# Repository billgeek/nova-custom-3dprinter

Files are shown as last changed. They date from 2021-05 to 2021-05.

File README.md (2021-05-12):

# "Nova"
Nova is an Ender 5 Plus inspired 3D printer. While I "borrowed" some ideas of the movements, I designed the entire printer using Sketchup.



## Specifications
- Build volume: 310mm x 310mm x 350mm
- TMC2209 step motor drivers
- 0.9 degree NEMA17 stepper motors (X and Y axes)
- Direct Drive assembly 
- SKR 1.4 Turbo mainboard
- TFT35 Touch Screen display
- External MOSFET components to power the hotend and the heated bed
- Sensorless homing

## Bill of Materials
See the below Google Sheet for the bill of materials:

https://docs.google.com/spreadsheets/d/1B5keSqVwSLgc5OjsFatlqAnYNtMWsLssTLB85XMptbM/edit?usp=sharing

## Build Process
You can find the build instructions in this repo at the following location:
https://github.com/billgeek/nova-custom-3dprinter/tree/main/Build%20Instructions

Alternatively you can follow the Google Docs version of the same instructions:
https://docs.google.com/document/d/1tVqh7jPagdjaWtX-vD9JAcbRu_ECWRMzhDe-mzgvMuw/edit?usp=sharing

## Printed Parts
Please refer to the Bill of Materials sheet linked above for a list of printed parts. The STL files can be found here:
https://github.com/billgeek/nova-custom-3dprinter/tree/main/STL

## Firmware
I used the 2.0.x branch of Marlin when building the firmware for the printer. The configuration files are stored here in this repository.

## Gallery
I've uploaded a few pics to Google Photos during and after the build:

https://photos.app.goo.gl/cp9zkkoZYTewc5xc9

## Lessons Learned
This project taught me a lot of how printers and electronics work in general. Below are some takeaways I think are worth mentioning:
- Not all proximity sensors are made equal! The PL08-N sensors I received operate slightly differently than the standard "round" sensors and as such, I have the light permanently on due to disabling pull-up resistors.
- Squareness of the frame is critical. If your frame is not square, you will guaranteed not have decent quality. Use a T-square or something similar to ensure your build is perfectly square.
- On the SKR1.4, instead of using one driver for both Z motors, I decided to use E1 (second extruder) to drive the second Z motor. This is actually super easy to do, take a look at the included config.
- Instead of setting firmware to invert some axes, I decided to swap pins instead. Inverting in firmware works, but I didn't want to reflash yet again.
- ALWAYS make sure you test your ABL probe on a breadboard or any other way without connecting it to your printer. I had made a mistake with my initial voltage divider and measured 8V from the probe. Had this been installed, I would've fried my SKR!
- The power supply I ordered only has two DC outputs, so I chose to use one output for only the heated bed and the other for the hotend heater and the mainboard.
- The MOSFET modules are absolutely essential when using an SKR board. These boards have integrated MOSFETs for the heated bed and hotend, but they're rated at 10A max. With my bed at 240W and using 24V, that would put me right at the maximum current rating. I'd rather replace a $15 module than a $85 board!

## Still to do
There are a few things I have yet to fix:
- [ ] I need to install some drag chains so the "umbilical cord" stops dragging against the steel rods and to look somewhat better.
- [ ] Design a new electronics enclosure to move the box hanging from the side to the bottom, similar to the Ender 5 setup.
- [ ] Due to how the movements work, I can add Foamboard to the back, left and front with minimal effort to make an enclosure, but I'll still need to create a hood / roof for the X/Y axes.

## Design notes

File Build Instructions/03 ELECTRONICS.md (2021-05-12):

# Electronics

I'm not going to go into detail on how to install electronics for a 3D printer as there are so many detailed articles and videos on the subject available online. Instead, here's a quick to-do list of what I had to do:

- [ ] Install the hotend assembly and extruder of your choice. I went for an assembled Ender 3 hotend (future upgrade opportunity here!) and the Hero Me Gen 5 system with direct drive configuration found here: https://www.thingiverse.com/thing:4460970
- [ ] Optionally install your ABL, inductive probe, proximity sensor or BLTouch of choice.
- [ ] Print and install an electronics enclosure of your choice. There are plenty to choose from on Thingiverse, but I decided to use this one: https://www.thingiverse.com/thing:4338524
- [ ] Install your Mainboard and Mosfets into the enclosure.
- [ ] Wire up all five motors (X, Y, extruder and dual Z) to the mainboard.
- [ ] Print and install an LCD cover of your choice. There are plenty to choose from on Thingiverse, but I decided to use this one: https://www.thingiverse.com/thing:4547059
- [ ] Install your LCD into the cover, attach the cover to the frame and connect it to the mainboard.
- [ ] Wire your Power Supply to the mainboard and MOSFET boards.
- [ ] Connect your hotend and heated bed to the MOSFETs.
- [ ] Optionally connect your ABL to the mainboard.

If all went well, you should now have a semi-operational 3D printer!

The final step in the process would be to download, configure and flash the Firmware of your choice. I'm using Marlin and have included the configuration files I used in this repository.

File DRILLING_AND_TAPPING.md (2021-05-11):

# Drilling and Tapping

You will need to drill and tap holes into the aluminum extrusion. As this is not a handyman writeup but instead a 3D printer build instruction, I'll skip over  _how_ and focus on _what_.

## Materials

- [ ] 4 x 2040 Extrusion @ 500mm - Uprights
- [ ] 8 x 2020 Extrusion @ 500mm - Top and Bottom sides
- [ ] 1 x 2020 Extrusion @ 600mm - X Axis
- [ ] 2 x 2020 Extrusion @ 450mm - Bed Platform
- [ ] 2 x 2020 Extrusion @ 500mm - Bed Platform

### Uprights
**2040 Extrusion 500mm**
- Using an M5 tap, create threads for both center holes on one side and only one of the center holes on the other side. (3 tapped center holes)



### Top and Bottom Sides (only six pieces, leave 2 for later)
**2020 Extrusions 500mm**
- Drill an M5 hole in six of the 2020 500mm extrusions 10mm from either of the edges.



### X-Axis
**2020 Extrusion 600mm**
- From the left side, drill two M5 holes: one at 22mm and the other at 65mm. 
- From the right side, drill two  M5 holes: one at 25mm and the other at 65mm from the right edge.



### Bed Platform

Before we do the bed platform you will need to measure the distance from the center of the holes of your heated bed. This measurement will dictate where the holes will be that you need to drill. In my case, I measured **240mm**, so that's the value I'll use here.

**2020 Extrusion 500mm**
- Drill an M5 hole 10mm from either edge on both pieces. (2 holes total per piece)
- Drill an M4 hole 130mm from either edge. (Formula used: Bed Holes = 240mm apart; Length = 500mm, so remainder = 260mm / 2 = 130mm) This hole will be used for the bed screws.

(In the below picture, do NOT drill into your heated bed, this picture simply indciates where the holes are referred to above)



**2020 Extrusion 450mm**
- Drill two M5 holes at 10mm and at 30mm from the left edge and repeat from the right edge. (4 holes total per piece)
- Rotate the extrusion so the new holes will be perpendicular to the holes you have already drilled. (IE: The holes you drilled before should go front to back while the next set of holes are top to bottom)
- Drill two M5 holes 105mm from each side. (Formula used: Bed Holes = 240mm, so 450mm length - 240mm holes = 210mm / 2 = 105mm)
 


And that's all there is to drill and tap. Next you can start with the actual frame construction.

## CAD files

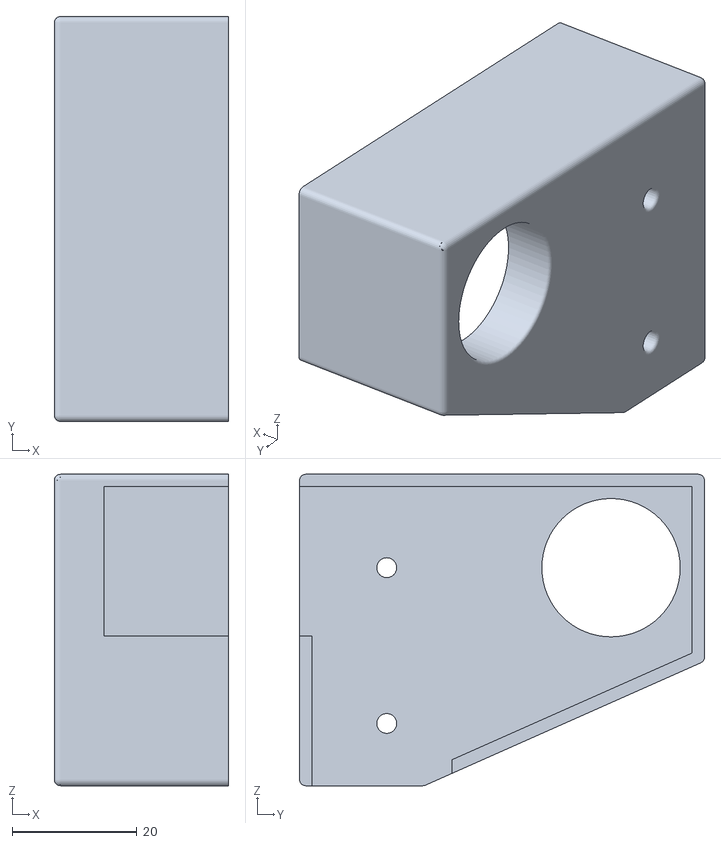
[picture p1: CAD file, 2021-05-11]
STL/YAxisCover.stl
28.0 x 65.0 x 50.0

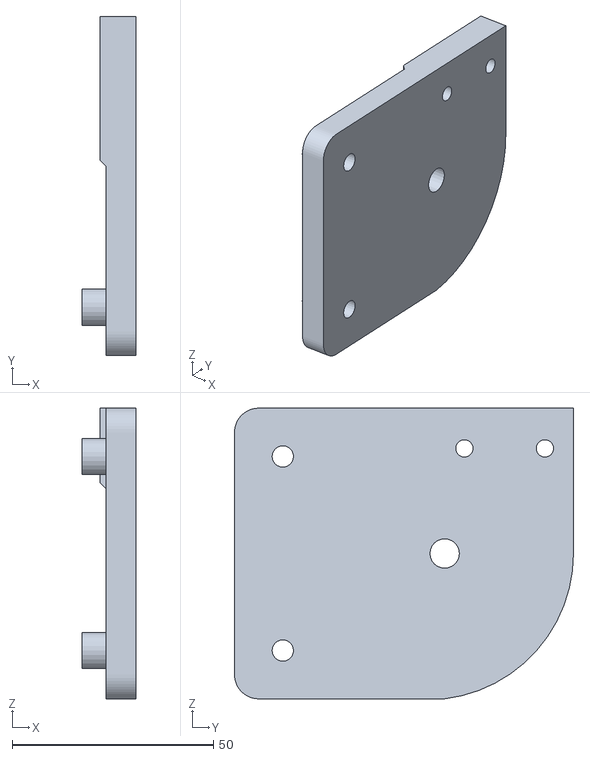
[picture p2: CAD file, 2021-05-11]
STL/ZAxisPlate.stl
13.5 x 84.2 x 72.2

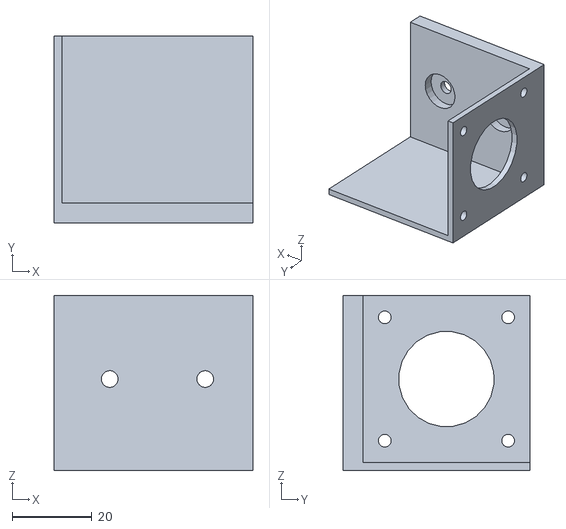
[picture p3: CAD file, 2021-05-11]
STL/YMotorBracket.stl
50.0 x 47.0 x 44.0

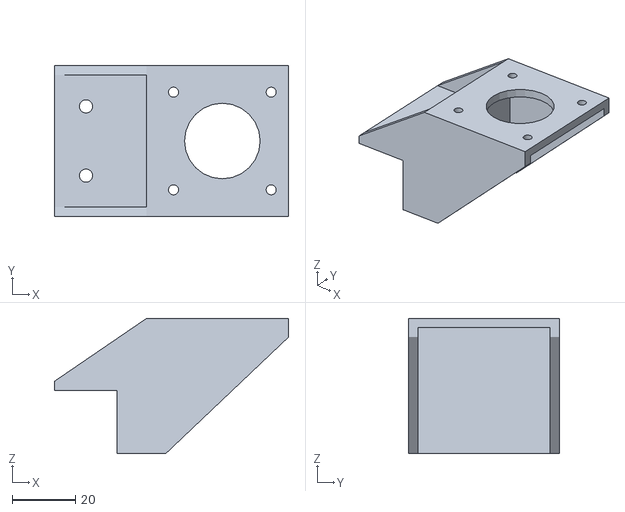
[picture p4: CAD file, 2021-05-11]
STL/ZMotorBracket.stl
74.3 x 48.0 x 43.0

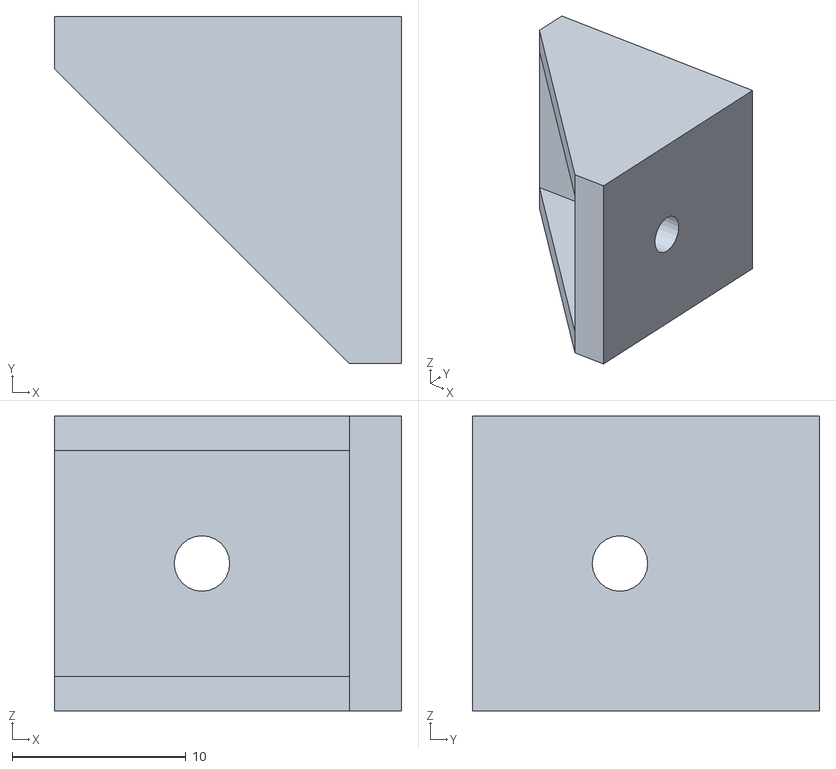
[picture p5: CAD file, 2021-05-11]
STL/UpperAngleBracket.stl
20.0 x 20.0 x 17.0

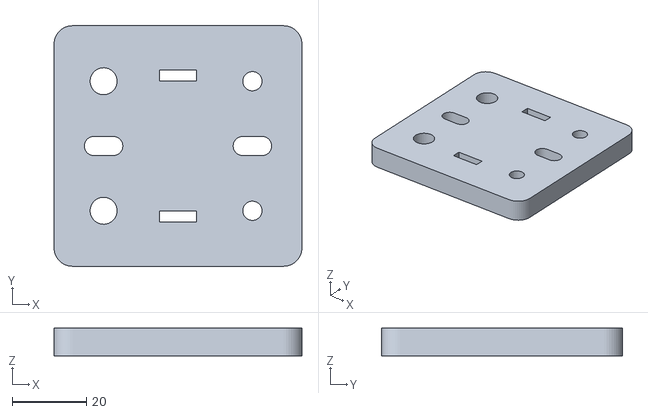
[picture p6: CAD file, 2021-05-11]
STL/XAxisGantryPlate.stl
67.0 x 65.0 x 7.50

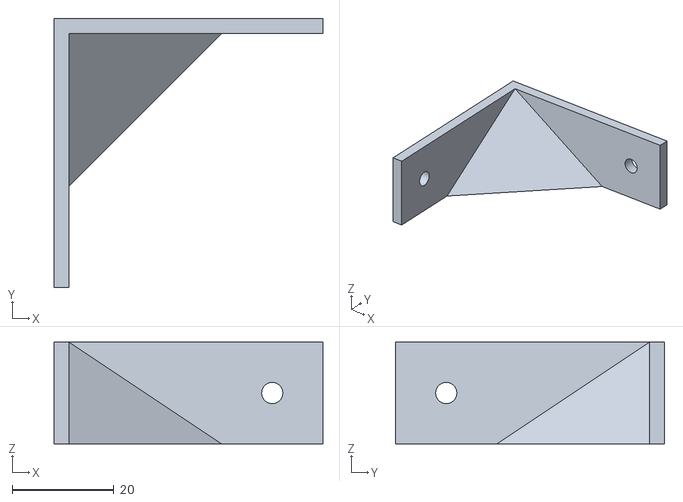
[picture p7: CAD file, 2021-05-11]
STL/LowerAngleBracket.stl
53.0 x 53.0 x 20.0

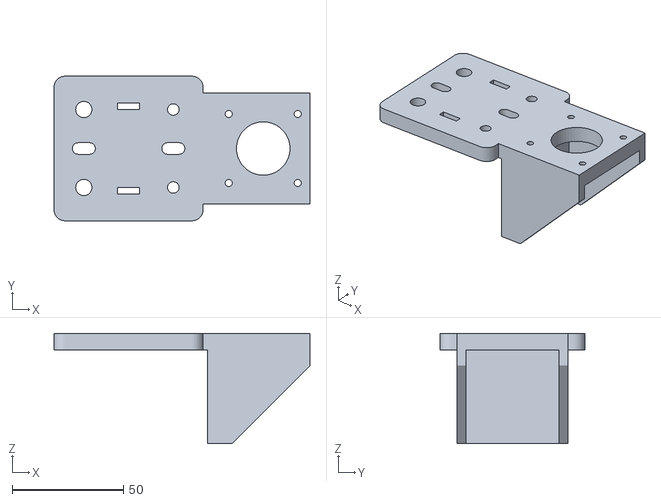
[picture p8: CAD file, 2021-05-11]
STL/XMotorBracket.stl
115.0 x 65.0 x 49.5

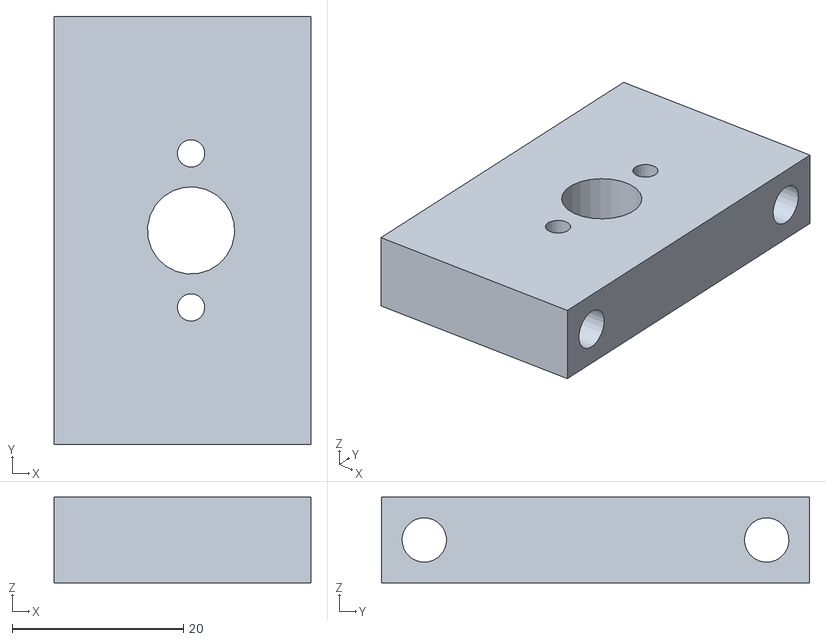
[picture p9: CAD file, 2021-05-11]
STL/LeadScrewNutHolder.stl
30.0 x 50.0 x 10.0

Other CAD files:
Sketchup/Ender 5 Clone.skp

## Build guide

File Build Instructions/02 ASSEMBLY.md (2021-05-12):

# Assembly

For the assembly we'll break it into six sections.

## Frame Base

To assemble the base of the frame:

- Arrange four 2020 extrusions in a square with the front and back between the left and right sides. You will end up with a build that is 540mm wide.
- Attach the four sides together using four printed LowerAngleBracket.stl and two M3x10mm bolts and M3 TNuts per corner.
- Attach the four 2040 extrusions to each corner (two tapped holes facing down AND the one tapped hole facing the inside) using 2 x M5x45mm bolts. Note that the wide sides should face towards the front of the printer.





## Upper Frame
- Arrange four 2020 extrusions in a square with the front and back between the left and right sides.
- Attach the four sides to each-other using the four UpperAngleBracket.stl two M3x10mm bolts and M3 TNuts per corner.
- Temporarily attach the upper frame to the rest of the frame using two M5x45mm bolts through the front and back sections into the tapped upright holes.
- Attach the YMotorBracket.stl to the center of the back section of the upper frame using two M3x10mm bolts and M3 TNuts.
- Attach your dual-shaft stepper motor to the bracket.









## X Axis
- Using the 600mm 2020 extrusion, attach it to the XMotorBracket.stl and XAxisGantryPlate.stl using 4 x M5x45mm bolts and nyloc nuts.
- Attach the stepper motor for the X movement to the motor bracket.
-  Add a toothed pulley to the X Motor.
- Add the hotend gantry plate to the extrusion bar. (You may have to either do this before attaching the X axis plate or remove a POM wheel to "clip" it on)
- Add a smooth pulley into one of the tensioner assemblies and unscrew the tensioner until you have the shortest possible distance. (IE: Allow yourself to pull the belt later)
- Holding the tensioner in place against the end of the X Axis, measure out a belt and attach the belt to the entire assembly.
- Attach four POM wheels to either side of the axis using two eccentric nuts per plate.
- Remove the top frame from the lower frame and slide the X axis over the sides. You may need to remove the "front" bar of the top frame to achieve this.
- Once the X axis is sliding on the top frame, attach the top frame back onto the bottom frame temporarily.





## Build Platform
- Using the remaining two 500mm 2020 extrusions and the two 400mm extrusions, place the shorter ones down and place the longer ones on top at a distance equal to the mounting holes of the bed.
- Attach all the extrusions together using M5 bolts. Do not install your bed yet as there's still work to do and you probably don't want to damage it.
- Attach the two LeadScrewNutHolder.stl to the sides using TNuts. Try to get them exactly in the center, but don't worry too much at this stage, you will likely adjust them later in the build process.
- Install three POM wheels on each of the four ZAxisPlate.stl, taking care to install the single wheel (under the "bump") using an eccentric nut.
- On each end of the sides of extrusion that are "sticking out", attach your assembled ZAxisPlate.stl using M5 bolts and nuts.
- Remove the top frame again and slide the entire bed frame over the corners.
- Once the Z axis is sliding on the corners, attach the top frame back onto the bottom frame temporarily. (Note that this might not be super easy, depending on how accurately you drilled the holes)





## Z Motors and Lead Screws
- Attach a stepper motor to both of the ZMotorBracket.stl
- Attach the stepper motor and bracket assembly to the center of each side on the bottom of the frame. Don't worry about getting this exactly in the center, you will likely have to adjust once the build is more complete.
- Install a coupler on each motor.
- Slide the lead screws through the top of the lead screw nut holder, through the anti-backlash nuts into the coupler. 
- Now move your build platform up and down to it's maximums to adjust everything to the center without tilting. Take your time here to make sure you get it right. I had to redo this a number of times as the build platform kept "tilting" after moving the Z axis down and up again.



## Y Axis
- Remove the top frame from the printer again.
- Insert a 608 bearing into each of the two YAxisCover.stl and set aside for now.
- Place a 5mm to 8mm coupler on each shaft coming out of the Y motor.
- Add a steel shaft to the other side of each coupler and add an 8mm toothed pulley to the other end of each shaft. (Try not to allow them to bend too far as this may cause damage to the couplers)
- With the shaft and pulley installed, attach the Y axis cover using a single M3x10mm bolt and TNut in the top-most hole and add the second M3x10 bolt and T-Nut in the lower hole without attaching it anywhere. Note that the shaft should run parallel to the top-back corner of the frame.
- Once you've installed the covers, install the belts in a similar fashion as you did for the X axis: Hold a tensioner in place against one of the front ends and measure out a belt and attach the belt to the respective gantry plate. Do this on both sides.
- Attach the entire X and Y axis assemblies to the rest of the printer frame using 4 x M5x45mm bolts.
- Complete the attaching of the YAxisCover.stl bottom screw into the side of the 2040 extrusion from the uprights.

## Final Touches
- Install your heated bed to the build platform using the tapered M4 screws, springs and levelling knobs of your choice. (You can either purchase some or find some available on Thingiverse)

Congratulations, you have completed the build! Up next is the Electronics.

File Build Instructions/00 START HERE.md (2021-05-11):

# Nova Custom 3D Printer Build Instructions

There are three main categories to the build instructions, each with a set of steps to complete: Drilling and Tapping, Assembly and Electronics.

Follow each of the links below for a complete assembly:

## Drilling and Tapping

Find the drilling and tapping instructions here: https://github.com/billgeek/nova-custom-3dprinter/blob/main/Build%20Instructions/01%20DRILLING_AND_TAPPING.md

## Assembly

Instructions for assembling all mechanical parts can be found here: https://github.com/billgeek/nova-custom-3dprinter/blob/main/Build%20Instructions/02%20ASSEMBLY.md

## Electronics

There are no detailed instructions for the electronics, but here's a simple to-do list of tasks that need to be completed: https://github.com/billgeek/nova-custom-3dprinter/blob/main/Build%20Instructions/03%20ELECTRONICS.md

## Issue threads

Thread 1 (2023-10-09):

BOM is no longer a valid link

pilotkid, 2023-10-09:
The bill of materials link is broken

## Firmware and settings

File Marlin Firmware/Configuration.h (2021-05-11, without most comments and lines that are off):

#pragma once
#define CONFIGURATION_H_VERSION 020008
#define STRING_CONFIG_H_AUTHOR "(BillGeek, SKR 1.4 Turbo)" // Who made the changes.
#define SHOW_BOOTSCREEN
#define SERIAL_PORT 0
#define SERIAL_PORT_2 -1
#define BAUDRATE 115200
  #define MOTHERBOARD BOARD_BTT_SKR_V1_4_TURBO
#define CUSTOM_MACHINE_NAME "BillGeek Ender 5 Clone"
#define EXTRUDERS 1
#define DEFAULT_NOMINAL_FILAMENT_DIA 1.75
#define TEMP_SENSOR_0 1
#define TEMP_SENSOR_1 0
#define TEMP_SENSOR_2 0
#define TEMP_SENSOR_3 0
#define TEMP_SENSOR_4 0
#define TEMP_SENSOR_5 0
#define TEMP_SENSOR_6 0
#define TEMP_SENSOR_7 0
#define TEMP_SENSOR_BED 1
#define TEMP_SENSOR_PROBE 0
#define TEMP_SENSOR_CHAMBER 0
#define DUMMY_THERMISTOR_998_VALUE  25
#define DUMMY_THERMISTOR_999_VALUE 100
#define MAX_REDUNDANT_TEMP_SENSOR_DIFF 10
#define TEMP_RESIDENCY_TIME     10  // (seconds) Time to wait for hotend to "settle" in M109
#define TEMP_WINDOW              1  // (°C) Temperature proximity for the "temperature reached" timer
#define TEMP_HYSTERESIS          3  // (°C) Temperature proximity considered "close enough" to the target
#define TEMP_BED_RESIDENCY_TIME 10  // (seconds) Time to wait for bed to "settle" in M190
#define TEMP_BED_WINDOW          1  // (°C) Temperature proximity for the "temperature reached" timer
#define TEMP_BED_HYSTERESIS      3  // (°C) Temperature proximity considered "close enough" to the target
#define HEATER_0_MINTEMP   5
#define HEATER_1_MINTEMP   5
#define HEATER_2_MINTEMP   5
#define HEATER_3_MINTEMP   5
#define HEATER_4_MINTEMP   5
#define HEATER_5_MINTEMP   5
#define HEATER_6_MINTEMP   5
#define HEATER_7_MINTEMP   5
#define BED_MINTEMP        5
#define HEATER_0_MAXTEMP 275
#define HEATER_1_MAXTEMP 275
#define HEATER_2_MAXTEMP 275
#define HEATER_3_MAXTEMP 275
#define HEATER_4_MAXTEMP 275
#define HEATER_5_MAXTEMP 275
#define HEATER_6_MAXTEMP 275
#define HEATER_7_MAXTEMP 275
#define BED_MAXTEMP      150
#define PIDTEMP
#define BANG_MAX 255     // Limits current to nozzle while in bang-bang mode; 255=full current
#define PID_MAX BANG_MAX // Limits current to nozzle while PID is active (see PID_FUNCTIONAL_RANGE below); 255=full current
#define PID_K1 0.95      // Smoothing factor within any PID loop
    #define DEFAULT_Kp  22.73
    #define DEFAULT_Ki   1.81
    #define DEFAULT_Kd  71.43
#define MAX_BED_POWER 255 // limits duty cycle to bed; 255=full current
  #define PID_FUNCTIONAL_RANGE 10 // If the temperature difference between the target temperature and the actual temperature
#define PREVENT_COLD_EXTRUSION
#define EXTRUDE_MINTEMP 170
#define PREVENT_LENGTHY_EXTRUDE
#define EXTRUDE_MAXLENGTH 200
#define THERMAL_PROTECTION_HOTENDS // Enable thermal protection for all extruders
#define THERMAL_PROTECTION_BED     // Enable thermal protection for the heated bed
#define THERMAL_PROTECTION_CHAMBER // Enable thermal protection for the heated chamber
#define USE_XMIN_PLUG
#define USE_YMIN_PLUG
#define USE_ZMIN_PLUG
#define ENDSTOPPULLUPS
#define X_MIN_ENDSTOP_INVERTING false // Set to true to invert the logic of the endstop.
#define Y_MIN_ENDSTOP_INVERTING false // Set to true to invert the logic of the endstop.
#define Z_MIN_ENDSTOP_INVERTING true // Set to true to invert the logic of the endstop.
#define X_MAX_ENDSTOP_INVERTING false // Set to true to invert the logic of the endstop.
#define Y_MAX_ENDSTOP_INVERTING false // Set to true to invert the logic of the endstop.
#define Z_MAX_ENDSTOP_INVERTING false // Set to true to invert the logic of the endstop.
#define Z_MIN_PROBE_ENDSTOP_INVERTING true // Set to true to invert the logic of the probe.
#define X_DRIVER_TYPE  TMC2209
#define Y_DRIVER_TYPE  TMC2209
#define Z_DRIVER_TYPE  TMC2209
#define Z2_DRIVER_TYPE TMC2209
#define E0_DRIVER_TYPE TMC2209
#define DEFAULT_AXIS_STEPS_PER_UNIT   { 160, 160, 400, 143 }
#define DEFAULT_MAX_FEEDRATE          { 300, 300, 5, 25 }
#define DEFAULT_MAX_ACCELERATION      { 3000, 3000, 100, 10000 }
#define DEFAULT_ACCELERATION          3000    // X, Y, Z and E acceleration for printing moves
#define DEFAULT_RETRACT_ACCELERATION  3000    // E acceleration for retracts
#define DEFAULT_TRAVEL_ACCELERATION   3000    // X, Y, Z acceleration for travel (non printing) moves
#define DEFAULT_EJERK    5.0  // May be used by Linear Advance
  #define JUNCTION_DEVIATION_MM 0.08 // (mm) Distance from real junction edge
  #define JD_HANDLE_SMALL_SEGMENTS    // Use curvature estimation instead of just the junction angle
#define Z_MIN_PROBE_USES_Z_MIN_ENDSTOP_PIN
#define USE_PROBE_FOR_Z_HOMING
#define FIX_MOUNTED_PROBE
#define NOZZLE_TO_PROBE_OFFSET { 10, 10, -4.75 }
#define PROBING_MARGIN 60
#define XY_PROBE_SPEED (133*60)
#define Z_PROBE_SPEED_FAST (4*60)
#define Z_PROBE_SPEED_SLOW (Z_PROBE_SPEED_FAST / 2)
#define MULTIPLE_PROBING 2
#define Z_CLEARANCE_DEPLOY_PROBE   10 // Z Clearance for Deploy/Stow
#define Z_CLEARANCE_BETWEEN_PROBES  5 // Z Clearance between probe points
#define Z_CLEARANCE_MULTI_PROBE     5 // Z Clearance between multiple probes
#define Z_PROBE_LOW_POINT          -2 // Farthest distance below the trigger-point to go before stopping
#define Z_PROBE_OFFSET_RANGE_MIN -20
#define Z_PROBE_OFFSET_RANGE_MAX 20
#define X_ENABLE_ON 0
#define Y_ENABLE_ON 0
#define Z_ENABLE_ON 0
#define E_ENABLE_ON 0 // For all extruders
#define DISABLE_X false
#define DISABLE_Y false
#define DISABLE_Z false
#define DISABLE_E false             // Disable the extruder when not stepping
#define DISABLE_INACTIVE_EXTRUDER   // Keep only the active extruder enabled
#define INVERT_X_DIR false
#define INVERT_Y_DIR true
#define INVERT_Z_DIR false
#define INVERT_E0_DIR false
#define INVERT_E1_DIR false
#define INVERT_E2_DIR false
#define INVERT_E3_DIR false
#define INVERT_E4_DIR false
#define INVERT_E5_DIR false
#define INVERT_E6_DIR false
#define INVERT_E7_DIR false
#define X_HOME_DIR -1
#define Y_HOME_DIR -1
#define Z_HOME_DIR -1
#define X_BED_SIZE 300
#define Y_BED_SIZE 300
#define X_MIN_POS -30
#define Y_MIN_POS 0
#define Z_MIN_POS 0
#define X_MAX_POS X_BED_SIZE
#define Y_MAX_POS Y_BED_SIZE
#define Z_MAX_POS 350
#define MIN_SOFTWARE_ENDSTOPS
  #define MIN_SOFTWARE_ENDSTOP_X
  #define MIN_SOFTWARE_ENDSTOP_Y
  #define MIN_SOFTWARE_ENDSTOP_Z
#define MAX_SOFTWARE_ENDSTOPS
  #define MAX_SOFTWARE_ENDSTOP_X
  #define MAX_SOFTWARE_ENDSTOP_Y
  #define MAX_SOFTWARE_ENDSTOP_Z
#define AUTO_BED_LEVELING_BILINEAR
#define PREHEAT_BEFORE_LEVELING
  #define LEVELING_NOZZLE_TEMP 120   // (°C) Only applies to E0 at this time
  #define LEVELING_BED_TEMP     50
  #define ENABLE_LEVELING_FADE_HEIGHT
    #define DEFAULT_LEVELING_FADE_HEIGHT 10.0 // (mm) Default fade height.
  #define SEGMENT_LEVELED_MOVES
  #define LEVELED_SEGMENT_LENGTH 5.0 // (mm) Length of all segments (except the last one)
  #define GRID_MAX_POINTS_X 5
  #define GRID_MAX_POINTS_Y GRID_MAX_POINTS_X
#define Z_SAFE_HOMING
  #define Z_SAFE_HOMING_X_POINT X_CENTER  // X point for Z homing
  #define Z_SAFE_HOMING_Y_POINT Y_CENTER  // Y point for Z homing
#define HOMING_FEEDRATE_MM_M { (50*60), (50*60), (4*60) }
#define VALIDATE_HOMING_ENDSTOPS
#define EEPROM_SETTINGS     // Persistent storage with M500 and M501
#define EEPROM_CHITCHAT       // Give feedback on EEPROM commands. Disable to save PROGMEM.
#define EEPROM_BOOT_SILENT    // Keep M503 quiet and only give errors during first load
#define HOST_KEEPALIVE_FEATURE        // Disable this if your host doesn't like keepalive messages
#define DEFAULT_KEEPALIVE_INTERVAL 2  // Number of seconds between "busy" messages. Set with M113.
#define BUSY_WHILE_HEATING            // Some hosts require "busy" messages even during heating
#define PREHEAT_1_LABEL       "PLA"
#define PREHEAT_1_TEMP_HOTEND 180
#define PREHEAT_1_TEMP_BED     70
#define PREHEAT_1_FAN_SPEED     0 // Value from 0 to 255
#define PREHEAT_2_LABEL       "ABS"
#define PREHEAT_2_TEMP_HOTEND 240
#define PREHEAT_2_TEMP_BED    110
#define PREHEAT_2_FAN_SPEED     0 // Value from 0 to 255
#define PRINTJOB_TIMER_AUTOSTART
#define LCD_LANGUAGE en
#define DISPLAY_CHARSET_HD44780 JAPANESE
#define LCD_INFO_SCREEN_STYLE 0
#define SDSUPPORT
#define REPRAP_DISCOUNT_FULL_GRAPHIC_SMART_CONTROLLER
#define SOFT_PWM_SCALE 0
#define SERVO_DELAY { 300 }

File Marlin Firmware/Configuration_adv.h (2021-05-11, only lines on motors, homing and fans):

#define E0_AUTO_FAN_PIN -1
#define E1_AUTO_FAN_PIN -1
#define E2_AUTO_FAN_PIN -1
#define E3_AUTO_FAN_PIN -1
#define E4_AUTO_FAN_PIN -1
#define E5_AUTO_FAN_PIN -1
#define E6_AUTO_FAN_PIN -1
#define E7_AUTO_FAN_PIN -1
#define CHAMBER_AUTO_FAN_PIN -1
#define HOMING_BUMP_MM      { 5, 5, 2 }       // (mm) Backoff from endstops after first bump
#define HOMING_BUMP_DIVISOR { 2, 2, 4 }       // Re-Bump Speed Divisor (Divides the Homing Feedrate)
  #define HOME_AFTER_G34
#define MICROSTEP_MODES { 16, 16, 16, 16, 16, 16 } // [1,2,4,8,16]
#define LIN_ADVANCE
  #define LIN_ADVANCE_K 0.22    // Unit: mm compression per 1mm/s extruder speed
    #define X_CURRENT       800        // (mA) RMS current. Multiply by 1.414 for peak current.
    #define X_CURRENT_HOME  X_CURRENT  // (mA) RMS current for sensorless homing
    #define X_MICROSTEPS     16        // 0..256
    #define Y_CURRENT       800
    #define Y_CURRENT_HOME  Y_CURRENT
    #define Y_MICROSTEPS     16
    #define Z_CURRENT       800
    #define Z_CURRENT_HOME  Z_CURRENT
    #define Z_MICROSTEPS     16
    #define Z2_CURRENT      800
    #define Z2_CURRENT_HOME Z2_CURRENT
    #define Z2_MICROSTEPS    16
    #define E0_CURRENT      800
    #define E0_MICROSTEPS    16
    #define CURRENT_STEP_DOWN     50  // [mA]
    #define REPORT_CURRENT_CHANGE
  #define X_HYBRID_THRESHOLD     100  // [mm/s]
  #define X2_HYBRID_THRESHOLD    100
  #define Y_HYBRID_THRESHOLD     100
  #define Y2_HYBRID_THRESHOLD    100
  #define Z_HYBRID_THRESHOLD       3
  #define Z2_HYBRID_THRESHOLD      3
  #define Z3_HYBRID_THRESHOLD      3
  #define Z4_HYBRID_THRESHOLD      3
  #define E0_HYBRID_THRESHOLD     30
  #define E1_HYBRID_THRESHOLD     30
  #define E2_HYBRID_THRESHOLD     30
  #define E3_HYBRID_THRESHOLD     30
  #define E4_HYBRID_THRESHOLD     30
  #define E5_HYBRID_THRESHOLD     30
  #define E6_HYBRID_THRESHOLD     30
  #define E7_HYBRID_THRESHOLD     30
  #define SENSORLESS_HOMING // StallGuard capable drivers only
    #define X_STALL_SENSITIVITY  128
    #define X2_STALL_SENSITIVITY X_STALL_SENSITIVITY
    #define Y_STALL_SENSITIVITY  128
    #define Y2_STALL_SENSITIVITY Y_STALL_SENSITIVITY

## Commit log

2021-04-08 Updated Stuff
    [Ender 5 Clone.skp, PSU Fan Bracket.stl, PSU to Socket Adapter.stl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]
2021-04-29 Remove marlin and keep configs
    [Configuration.h, Configuration_adv.h, Ender 5 Clone.skp]
2021-05-11 Working on readmes
    [Bottom Corner Bracket.stl, Cable Chain Cover.stl, Cable Chain.skp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]
2021-05-11 Drilling and Tapping
2021-05-11 STL's and more readmes
    [Cable Chain Cover.stl, Cable Chain.stl, Lead Screw Holder.stl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]
2021-05-11 Update 02 ASSEMBLY.md
2021-05-11 Update configuration
    [Configuration.h, Configuration_adv.h]

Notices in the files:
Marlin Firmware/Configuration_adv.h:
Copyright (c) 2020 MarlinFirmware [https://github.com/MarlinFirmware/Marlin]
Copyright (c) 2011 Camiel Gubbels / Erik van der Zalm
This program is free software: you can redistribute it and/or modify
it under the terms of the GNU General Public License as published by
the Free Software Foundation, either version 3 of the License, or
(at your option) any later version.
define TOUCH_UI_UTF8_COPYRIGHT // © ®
